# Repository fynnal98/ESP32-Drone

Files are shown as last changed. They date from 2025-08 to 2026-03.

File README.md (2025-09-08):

# ESP32-Drone
## Project Images



 

---
## Software
The code is structurd in modules:

**main**  
- Init: SBUS, IMU, PWM, LED, Battery  
- Safety: Failsafe, Low-voltage, Arming  
- Motor mix: Inputs + PID corrections  
**SbusReceiver**  
- Reads SBUS signal  
- Maps + filters channels  
- Deadband, scaling, failsafe check  

**MPU6050**  
- Reads gyro + accel  
- Complementary filter for roll/pitch  
- Provides orientation data  

**PidController**  
- Generic PID loop  
- Used for roll and pitch stabilization  (no yaw!)

**FlightController**  
- Reads roll/pitch targets from SBUS and actual values from IMU  
- Runs PID controllers for roll and pitch  
- Outputs correction values (but the Donelogic is used in main yet.)

**config.h**  
- Pin definitions  
- PID parameters  
- PWM setup  
- Battery thresholds 

---
## Hardware

Hardware:  
- ESP32-C3  
- MPU6050 // MPU6500  
- SBUS Receiver (serial data from RadioLink remote controller)  
- 4 × Brushed DC Motors (3.7 V)  
- Custom Motor Drivers (MOSFET + gate resistor + pull-down + Schottky diode)  
- 1S LiPo Battery  
- Resistor Divider (for battery voltage measurement)  
- LED Indicator (low-voltage warning)  
- Capacitors for voltage spikes  

The system is based on an ESP32-C3 Super Mini microcontroller combined with an MPU6500 IMU for orientation sensing.  
Remote control signals are received by a serial SBUS input.  
Four DC brushed motors are controlled by custom motor drivers. Each is build with a Mosfet, pulldown resisitor and a shottky diode.

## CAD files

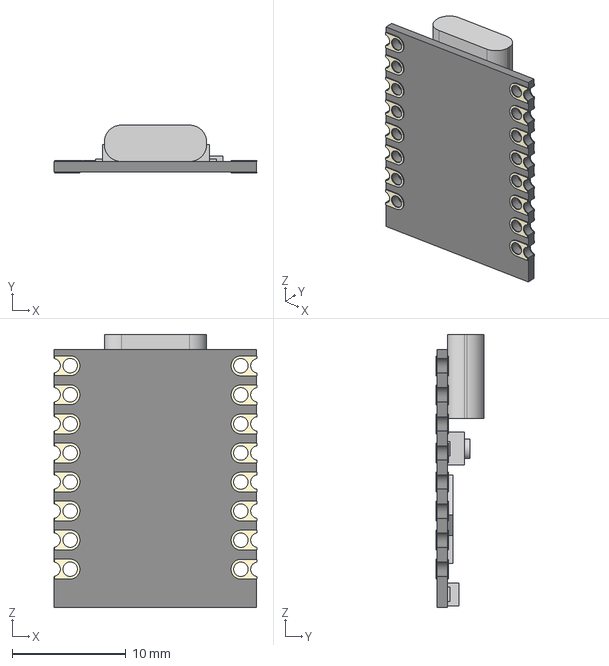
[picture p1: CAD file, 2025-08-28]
Hardware/CAD/V4/extern/ESP32-C3 supermini v5/ESP32-C3 supermini v5.step
17.8 x 4.20 x 24.0 mm

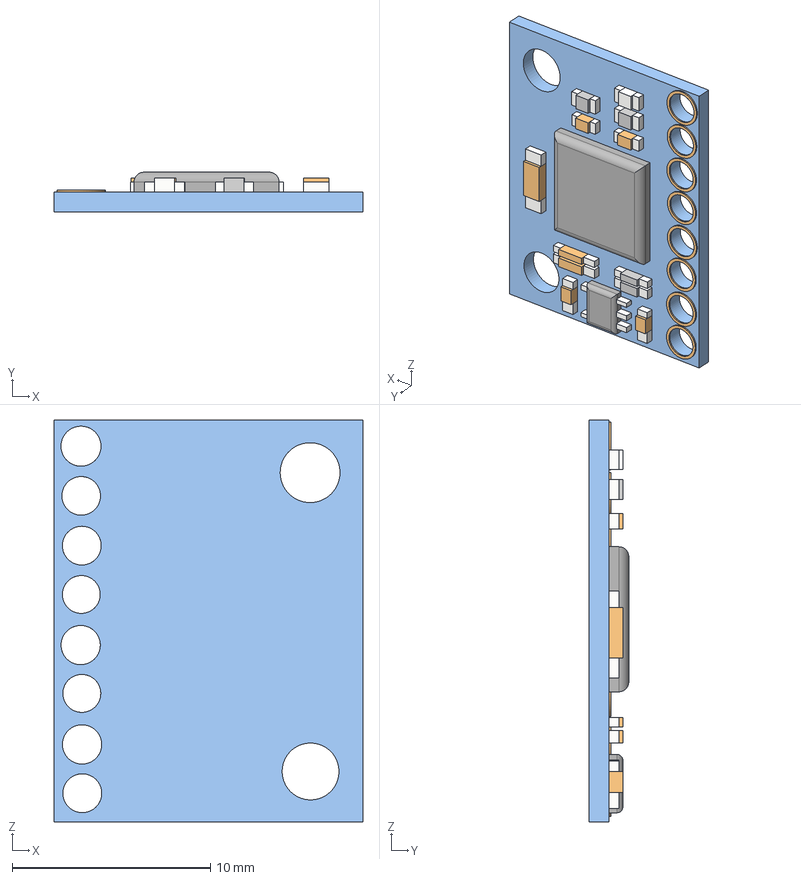
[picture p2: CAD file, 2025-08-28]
Hardware/CAD/V4/extern/MPU6050 v2/MPU6050 v2.step
15.6 x 2.00 x 20.3 mm

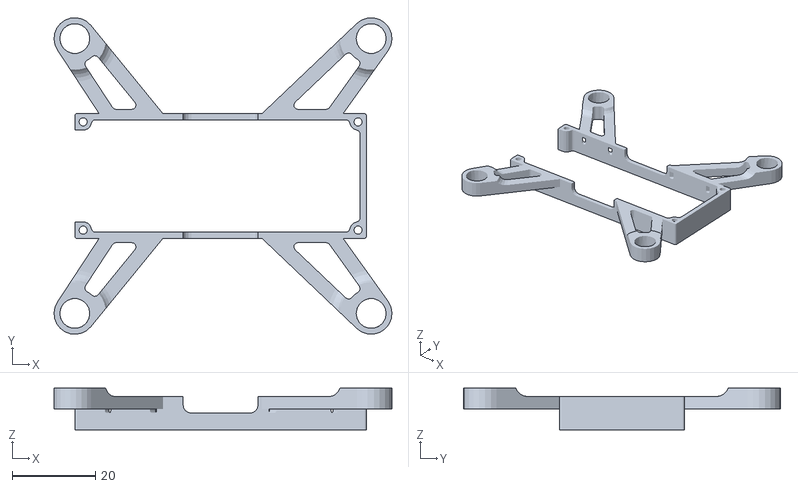
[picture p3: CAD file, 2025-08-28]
Hardware/CAD/V4/print/P_DroneCase.stl
81.1 x 76.0 x 10.0

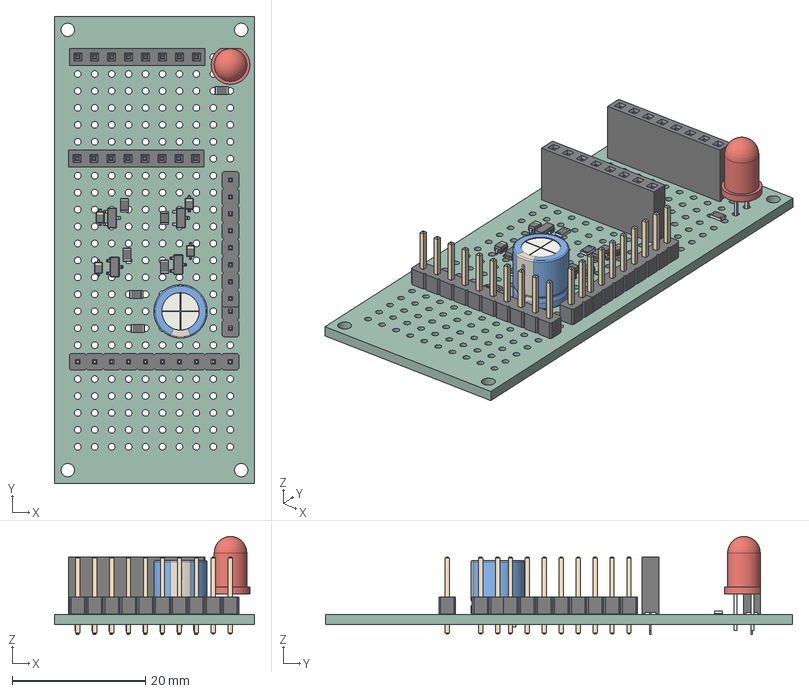
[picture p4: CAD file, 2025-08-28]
Hardware/PCB/MiniDroneFlightcontroller/MiniDroneFlightcontroller.step
30.0 x 70.0 x 14.7 mm
SOT-23 x 4
R_0805_2012Metric x 7
D_SOD-323 x 4
PinSocket_1x08_P2.54mm_Vertical x 2
CP_Radial_D8.0mm_P5.00mm
PinHeader_1x02_P2.54mm_Vertical
LED_D5.0mm
PinHeader_1x10_P2.54mm_Vertical
PinHeader_1x08_P2.54mm_Vertical
MiniDroneFlightcontroller_PCB

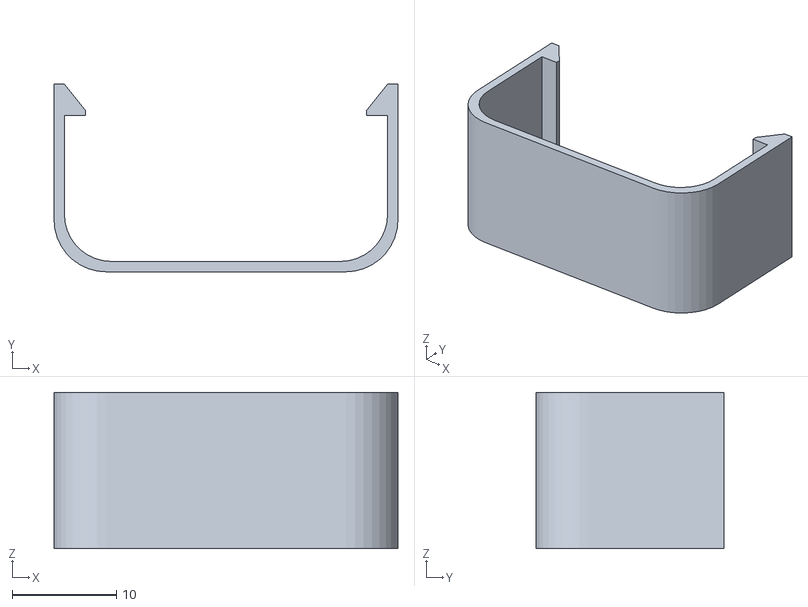
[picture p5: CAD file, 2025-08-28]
Hardware/CAD/V4/print/P_Halter.stl
33.0 x 18.0 x 15.0

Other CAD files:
Hardware/CAD/V1/OldVersions/A_MiniDrone.0048.iam
Hardware/CAD/V1/OldVersions/P_Akku_1S.0003.ipt
Hardware/CAD/V1/OldVersions/P_DroneCase.0054.ipt
Hardware/CAD/V1/P_Prop.ipt
Hardware/CAD/V2/OldVersions/A_MiniDrone.0068.iam
Hardware/CAD/V2/OldVersions/P_DroneCase.0111.ipt
Hardware/CAD/V2/OldVersions/P_Halter.0005.ipt
Hardware/CAD/V2/P_Prop.ipt
Hardware/CAD/V3/A_MiniDrone.iam
Hardware/CAD/V3/OldVersions/A_MiniDrone.0080.iam
Hardware/CAD/V3/OldVersions/P_Akku_1S.0004.ipt
Hardware/CAD/V3/OldVersions/P_DroneCase.0149.ipt
Hardware/CAD/V3/OldVersions/P_Halter.0007.ipt
Hardware/CAD/V3/OldVersions/P_Prop.0006.ipt
Hardware/CAD/V3/OldVersions/P_Prop_4_blade.0007.ipt
Hardware/CAD/V3/OldVersions/P_R6DSM.0010.ipt
Hardware/CAD/V3/P_Akku_1S.ipt
Hardware/CAD/V3/P_DroneCase.ipt
Hardware/CAD/V3/P_Halter.ipt
Hardware/CAD/V3/P_Motor.ipt
Hardware/CAD/V3/P_Motordriver.ipt
Hardware/CAD/V3/P_Prop_4_blade.ipt
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

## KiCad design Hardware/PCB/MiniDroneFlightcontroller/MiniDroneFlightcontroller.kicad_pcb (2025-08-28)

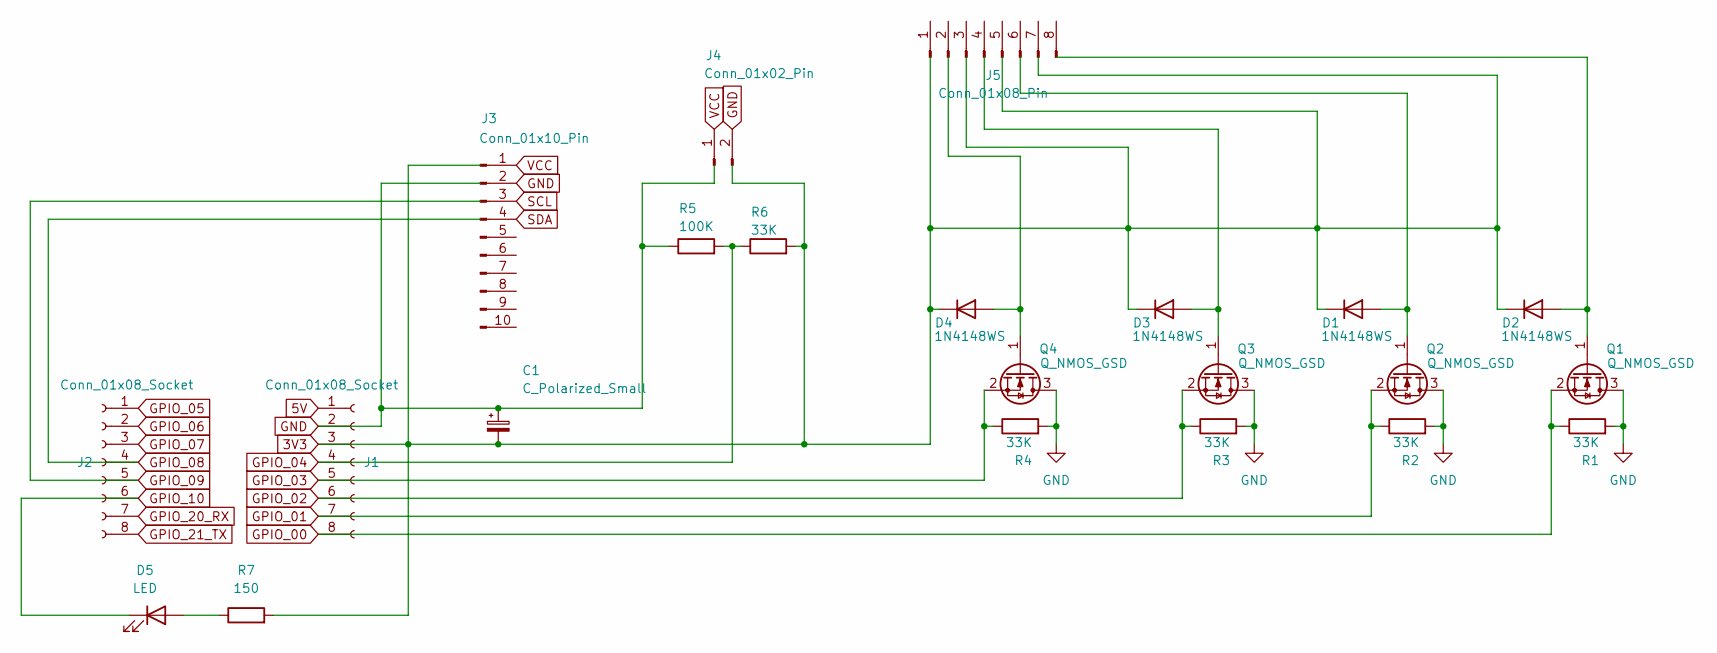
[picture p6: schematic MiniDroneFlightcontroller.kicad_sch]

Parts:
C1: C_Polarized_Small; CP_Radial_D8.0mm_P5.00mm
D1, D2, D3, D4: 1N4148WS; D_SOD-323
D5: LED; LED_D4.0mm
J1, J2: Conn_01x08_Socket; PinSocket_1x08_P2.54mm_Vertical
J3: Conn_01x10_Pin; PinHeader_1x10_P2.54mm_Vertical
J4: Conn_01x02_Pin; PinHeader_1x02_P2.54mm_Vertical
J5: Conn_01x08_Pin; PinHeader_1x08_P2.54mm_Vertical
Q1, Q2, Q3, Q4: Q_NMOS_GSD; SOT-23
R1, R2, R3, R4, R6: 33K; R_0805_2012Metric
R5: 100K; R_0805_2012Metric
R7: 150; R_0805_2012Metric

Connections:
3V3: C1.2, D1.1 (K), D2.1 (K), D3.1 (K), D4.1 (K), J1.3, R6.2, R7.2
5V: J1.1
GND: C1.1, J1.2, J3.2, J4.2, Q1.3 (D), Q2.3 (D), Q3.3 (D), Q4.3 (D), R1.2, R2.2, R3.2, R4.2, R5.1
GPIO_00: J1.8, Q1.2 (S), R1.1
GPIO_01: J1.7, Q2.2 (S), R2.1
GPIO_02: J1.6, Q3.2 (S), R3.1
GPIO_03: J1.5, Q4.2 (S), R4.1
GPIO_04: J1.4, R5.2, R6.1
GPIO_05: J2.1
GPIO_06: J2.2
GPIO_07: J2.3
GPIO_08: J2.4
GPIO_09: J2.5
GPIO_10: D5.1 (K), J2.6
GPIO_20_RX: J2.7
GPIO_21_TX: J2.8
unnamed: D1.2 (A), Q2.1 (G)
unnamed: D2.2 (A), Q1.1 (G)
unnamed: D3.2 (A), Q3.1 (G)
unnamed: D4.2 (A), Q4.1 (G)
unnamed: D5.2 (A), R7.1
SCL: J3.3
SDA: J3.4
VCC: J3.1, J4.1

Board: 2 copper layers, 22 parts (0 on the bottom side), 14 nets, no tracks yet.

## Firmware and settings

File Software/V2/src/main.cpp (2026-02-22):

#include <Arduino.h>
#include "Config.h"
#include "SbusReceiver.h"
#include "Mpu6050.h"
#include "FlightController.h"

static SbusReceiver rc;
static Mpu6050 imu;
static FlightController fc;

static uint32_t lastMicros = 0;

// Level offsets (werden nach Boot-Delay gemittelt)
static float levelRollOffDeg = 0.0f;
static float levelPitchOffDeg = 0.0f;

static void motorsInit() {
  ledcSetup(PWM_CH_MOTOR1, PWM_FREQ, PWM_RES_BITS);
  ledcSetup(PWM_CH_MOTOR2, PWM_FREQ, PWM_RES_BITS);
  ledcSetup(PWM_CH_MOTOR3, PWM_FREQ, PWM_RES_BITS);
  ledcSetup(PWM_CH_MOTOR4, PWM_FREQ, PWM_RES_BITS);

  ledcAttachPin(PIN_MOTOR1, PWM_CH_MOTOR1);
  ledcAttachPin(PIN_MOTOR2, PWM_CH_MOTOR2);
  ledcAttachPin(PIN_MOTOR3, PWM_CH_MOTOR3);
  ledcAttachPin(PIN_MOTOR4, PWM_CH_MOTOR4);

  ledcWrite(PWM_CH_MOTOR1, 0);
  ledcWrite(PWM_CH_MOTOR2, 0);
  ledcWrite(PWM_CH_MOTOR3, 0);
  ledcWrite(PWM_CH_MOTOR4, 0);
}

static void motorsOff() {
  ledcWrite(PWM_CH_MOTOR1, 0);
  ledcWrite(PWM_CH_MOTOR2, 0);
  ledcWrite(PWM_CH_MOTOR3, 0);
  ledcWrite(PWM_CH_MOTOR4, 0);
}

static void motorsWrite(const MotorOutputs& m) {
  const uint32_t d1 = (uint32_t)(m.m1 * (float)PWM_MAX);
  const uint32_t d2 = (uint32_t)(m.m2 * (float)PWM_MAX);
  const uint32_t d3 = (uint32_t)(m.m3 * (float)PWM_MAX);
  const uint32_t d4 = (uint32_t)(m.m4 * (float)PWM_MAX);

  ledcWrite(PWM_CH_MOTOR1, d1);
  ledcWrite(PWM_CH_MOTOR2, d2);
  ledcWrite(PWM_CH_MOTOR3, d3);
  ledcWrite(PWM_CH_MOTOR4, d4);
}

static void bootDelayAndCalibrate() {
  // 1) Delay damit du die Drohne sauber hinlegen kannst
  const uint32_t waitMs = BOOT_WAIT_MS;
  Serial.printf("BOOT: Warte %lums zum Hinlegen...\n", (unsigned long)waitMs);
  uint32_t t0 = millis();
  while (millis() - t0 < waitMs) {
    motorsOff();
    delay(50);
  }

  // 2) Gyro kalibrieren (Drohne muss ruhig liegen)
  if (imu.isConnected()) {
    Serial.println("BOOT: Gyro Kalibrierung (ruhig liegen lassen)...");
    imu.calibrate(600);
    Serial.println("BOOT: Gyro Kalibrierung fertig");
  }

  // 3) Level-Offset mitteln (Roll/Pitch Null setzen)
  //    (nur sinnvoll, wenn rollDeg/pitchDeg aus Acc+Gyro kommen)
  if (imu.isConnected()) {
    Serial.println("BOOT: Level-Offset messen (still & level)...");
    const uint32_t levelMs = LEVEL_CAL_MS;
    uint32_t start = millis();
    uint32_t n = 0;
    float sumR = 0.0f, sumP = 0.0f;

    // kleine dt Updates, damit roll/pitch frisch sind
    uint32_t last = micros();
    while (millis() - start < levelMs) {
      uint32_t now = micros();
      float dt = (float)(now - last) / 1000000.0f;
      last = now;
      if (dt < DT_MIN) dt = DT_MIN;
      if (dt > DT_MAX) dt = DT_MAX;

      imu.update(dt);
      sumR += imu.rollDeg();
      sumP += imu.pitchDeg();
      n++;
      motorsOff();
      delay(5);
    }

    if (n > 0) {
      levelRollOffDeg = sumR / (float)n;
      levelPitchOffDeg = sumP / (float)n;
    }
    Serial.printf("BOOT: Level-Offset gesetzt rollOff=%.2f pitchOff=%.2f\n",
                  levelRollOffDeg, levelPitchOffDeg);
  }
}

void setup() {
  Serial.begin(115200);
  delay(200);

  motorsInit();
  rc.begin();

  const bool imuOk = imu.begin(IMU_SDA_PIN, IMU_SCL_PIN);
  if (!imuOk) {
    Serial.println("MPU6050 NICHT gefunden");
  } else {
    Serial.println("MPU6050 OK");
  }

  // PID config (falls du das nutzt)
  fc.setConfig(FC_CFG);
  fc.begin();

  bootDelayAndCalibrate();

  lastMicros = micros();
}

void loop() {
  const uint32_t nowUs = micros();
  const uint32_t periodUs = 1000000UL / LOOP_HZ;

  if ((uint32_t)(nowUs - lastMicros) < periodUs) {
    delayMicroseconds(30);
    return;
  }

  float dt = (float)(nowUs - lastMicros) / 1000000.0f;
  lastMicros = nowUs;
  if (dt < DT_MIN) dt = DT_MIN;
  if (dt > DT_MAX) dt = 1.0f / (float)LOOP_HZ;

  rc.update();

  if (rc.signalLost()) {
    motorsOff();
    fc.reset();
    return;
  }

  if (imu.isConnected()) {
    imu.update(dt);
  }

  static bool armed = false;
  const bool armSwitch = rc.armed();
  const float thr = rc.throttle();

  if (!armSwitch) {
    armed = false;
    motorsOff();
    fc.reset();
    return;
  }

  if (!armed) {
    motorsOff();
    fc.reset();
    if (thr < THROTTLE_MIN_ARM) {
      armed = true;
      fc.reset();
    }
    return;
  }

  if (thr < THR_CUTOFF) {
    motorsOff();
    fc.reset();
    return;
  }

  // WICHTIG: Offsets übergeben
const MotorOutputs m = fc.update(rc, imu, dt, armed, levelRollOffDeg, levelPitchOffDeg);  motorsWrite(m);

Serial.printf("Rlvl=%.2f Plvl=%.2f\n",
              imu.rollDeg() - levelRollOffDeg,
              imu.pitchDeg() - levelPitchOffDeg);
}

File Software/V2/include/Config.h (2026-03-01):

#pragma once
#include <stdint.h>

// === Boot / Calibration Timing ===
static constexpr uint32_t BOOT_WAIT_MS = 3000;        // Zeit zum Hinlegen nach Akku
static constexpr uint32_t LEVEL_CAL_MS = 1500;        // Dauer Level-Mittelung

/* =========================
 * SBUS
 * ========================= */
static constexpr int SBUS_RX_PIN     = 20;
static constexpr bool SBUS_INVERTED  = true;
static constexpr uint32_t SBUS_SIGNAL_TIMEOUT_MS = 300;

static constexpr int SBUS_INPUT_MIN = 307;
static constexpr int SBUS_INPUT_MAX = 1693;

/* Channel mapping (Radiolink typisch) */
static constexpr int CH_ROLL     = 0; // CH1
static constexpr int CH_PITCH    = 1; // CH2
static constexpr int CH_THROTTLE = 2; // CH3
static constexpr int CH_YAW      = 3; // CH4
static constexpr int CH_ARM      = 9; // AUX

/* RC shaping */
static constexpr float RC_DEADBAND     = 0.03f;
static constexpr float RC_SMOOTH_ALPHA = 0.85f;

/* =========================
 * IMU (MPU6050)
 * ========================= */
static constexpr int IMU_SDA_PIN = 6;
static constexpr int IMU_SCL_PIN = 7;

static constexpr float COMP_ALPHA = 0.98f;

/* =========================
 * Motors / Pins
 * ========================= */
static constexpr int PIN_MOTOR1 = 5;
static constexpr int PIN_MOTOR2 = 2;
static constexpr int PIN_MOTOR3 = 3;
static constexpr int PIN_MOTOR4 = 4;

/* =========================
 * PWM (LEDC) — dein funktionierendes Setup
 * ========================= */
static constexpr uint32_t PWM_FREQ     = 12000;
static constexpr uint8_t  PWM_RES_BITS = 10;
static constexpr uint32_t PWM_MAX      = (1u << PWM_RES_BITS) - 1u;

static constexpr int PWM_CH_MOTOR1 = 0;
static constexpr int PWM_CH_MOTOR2 = 1;
static constexpr int PWM_CH_MOTOR3 = 2;
static constexpr int PWM_CH_MOTOR4 = 3;

/* =========================
 * Control Loop
 * ========================= */
static constexpr uint32_t LOOP_HZ = 500;
static constexpr float DT_MIN = 1.0f / 2000.0f;
static constexpr float DT_MAX = 1.0f / 50.0f;

/* Stabilize */
static constexpr float MAX_ANGLE_DEG = 15.0f;

/* Rate limits */
static constexpr float MAX_RATE_ROLL_DPS  = 350.0f;
static constexpr float MAX_RATE_PITCH_DPS = 350.0f;
static constexpr float MAX_RATE_YAW_DPS   = 220.0f;

/* Safety */
static constexpr float THROTTLE_MIN_ARM = 0.02f; // arm nur bei low throttle
static constexpr float THR_CUTOFF       = 0.01f; // darunter: motor off + pid reset
static constexpr float THROTTLE_IDLE    = 0.050f; // erst aktiv wenn thr > cutoff
static constexpr float THROTTLE_MAX     = 0.95f; // headroom fürs Mixing

/* Mixer option */
static constexpr bool MIX_SWAP_FRONT_BACK = false;


// =========================
// PID Config (tunable)
// =========================
struct PidGains {
  float kp;
  float ki;
  float kd;
  float iLimit;
  float outLimit;
};

struct FcConfig {
  // Angle (outer loop) -> outputs desired rate in deg/s
  PidGains angleRoll;
  PidGains anglePitch;

  // Rate (inner loop) -> outputs normalized correction
  PidGains rateRoll;
  PidGains ratePitch;
  PidGains rateYaw;

  // Optional: scaling for corrections at low throttle
  float corrRampFullAtThr; // e.g. 0.35f means full corrections at ~35% throttle
};

static constexpr FcConfig FC_CFG = {
  /* angleRoll  */ { 5.5f, 0.0f, 0.06f, 40.0f, 220.0f },
  /* anglePitch */ { 5.5f, 0.0f, 0.06f, 40.0f, 220.0f },

                 /* { kp   , ki   , kd     , iLimit, outLimit } */
  /* rateRoll   */ { 0.85f, 0.10f, 0.0012f, 0.90f, 1.60f },
  /* ratePitch  */ { 0.85f, 0.10f, 0.0012f, 0.90f, 1.60f },
  /* rateYaw    */ { 0.08f, 0.05f, 0.0000f, 0.40f, 0.80f },

  /* corrRampFullAtThr */ 0.06f
};


static constexpr float MOTOR_ROLL_TRIM = -0.00f;

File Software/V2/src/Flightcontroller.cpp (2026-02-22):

#include "FlightController.h"

float FlightController::clampf(float v, float lo, float hi)
{
    if (v < lo) return lo;
    if (v > hi) return hi;
    return v;
}

void FlightController::setConfig(const FcConfig &cfg)
{
    _cfg = cfg;

    // Angle
    _pidAngleRoll.setGains(cfg.angleRoll.kp, cfg.angleRoll.ki, cfg.angleRoll.kd);
    _pidAngleRoll.setLimits(cfg.angleRoll.iLimit, cfg.angleRoll.outLimit);

    _pidAnglePitch.setGains(cfg.anglePitch.kp, cfg.anglePitch.ki, cfg.anglePitch.kd);
    _pidAnglePitch.setLimits(cfg.anglePitch.iLimit, cfg.anglePitch.outLimit);

    // Rate
    _pidRateRoll.setGains(cfg.rateRoll.kp, cfg.rateRoll.ki, cfg.rateRoll.kd);
    _pidRateRoll.setLimits(cfg.rateRoll.iLimit, cfg.rateRoll.outLimit);

    _pidRatePitch.setGains(cfg.ratePitch.kp, cfg.ratePitch.ki, cfg.ratePitch.kd);
    _pidRatePitch.setLimits(cfg.ratePitch.iLimit, cfg.ratePitch.outLimit);

    _pidRateYaw.setGains(cfg.rateYaw.kp, cfg.rateYaw.ki, cfg.rateYaw.kd);
    _pidRateYaw.setLimits(cfg.rateYaw.iLimit, cfg.rateYaw.outLimit);
}

void FlightController::begin()
{
    reset();
}

void FlightController::reset()
{
    _pidAngleRoll.reset();
    _pidAnglePitch.reset();

    _pidRateRoll.reset();
    _pidRatePitch.reset();
    _pidRateYaw.reset();
}

float FlightController::angleToRate(float angleSetDeg, float angleMeasDeg, Pid &anglePid, float dt)
{
    // output: deg/s
    return anglePid.update(angleSetDeg, angleMeasDeg, dt);
}

float FlightController::rateControl(float rateSetDps, float rateMeasDps, Pid &ratePid, float dt)
{
    // output: normalized correction (Mixer-Units)
    return ratePid.update(rateSetDps, rateMeasDps, dt);
}

MotorOutputs FlightController::update(SbusReceiver &rc,
                                      const Mpu6050 &imu,
                                      float dt,
                                      bool armed,
                                      float levelRollOffsetDeg,
                                      float levelPitchOffsetDeg)
{
    MotorOutputs out{};

    if (!armed)
    {
        return out;
    }

    // Throttle 0..1
    float thr = clampf(rc.throttle(), 0.0f, 1.0f);

    // Unter Cutoff: Motoren AUS + keine Regelung
    if (thr < THR_CUTOFF)
    {
        return out;
    }

    // Throttle auf Idle..THROTTLE_MAX skalieren (Headroom fürs Mixing)
    const float thrScaled = clampf(
        THROTTLE_IDLE + thr * (THROTTLE_MAX - THROTTLE_IDLE),
        0.0f, 1.0f);

    // Korrekturen bei niedrigem Throttle sanft hochfahren
    float rampDen = _cfg.corrRampFullAtThr;
    if (rampDen < 0.05f) rampDen = 0.05f; // Schutz
    float corrScale = (thr - THR_CUTOFF) / rampDen;
    corrScale = clampf(corrScale, 0.0f, 1.0f);

    // Stick -> Angle Sollwert (Angle Mode)
    const float rollSetDeg  = rc.roll()  * MAX_ANGLE_DEG;
    const float pitchSetDeg = rc.pitch() * MAX_ANGLE_DEG;

    // Gemessene Winkel (mit Level-Offset)
    const float rollMeasDeg  = imu.rollDeg()  - levelRollOffsetDeg;
    const float pitchMeasDeg = imu.pitchDeg() - levelPitchOffsetDeg;

    // Angle -> Rate Sollwerte (deg/s), begrenzen
    const float rollRateSet = clampf(
        angleToRate(rollSetDeg, rollMeasDeg, _pidAngleRoll, dt),
        -MAX_RATE_ROLL_DPS, MAX_RATE_ROLL_DPS);

    const float pitchRateSet = clampf(
        angleToRate(pitchSetDeg, pitchMeasDeg, _pidAnglePitch, dt),
        -MAX_RATE_PITCH_DPS, MAX_RATE_PITCH_DPS);

    // Yaw: direkt Rate Sollwert aus Stick
    const float yawRateSet = rc.yaw() * MAX_RATE_YAW_DPS;

    // Rate PIDs (Gyro rates)
    float rollCorr  = rateControl(rollRateSet,  imu.gyroX_dps(), _pidRateRoll,  dt);
    float pitchCorr = rateControl(pitchRateSet, imu.gyroY_dps(), _pidRatePitch, dt);
    float yawCorr   = rateControl(yawRateSet,   imu.gyroZ_dps(), _pidRateYaw,   dt);

    // Low-throttle scaling
    rollCorr  *= corrScale;
    pitchCorr *= corrScale;
    yawCorr   *= corrScale;
    
    rollCorr += MOTOR_ROLL_TRIM;


    // QUADX Mixer:
    // (m1..m4 sind "normalized motor commands" 0..1 nach clamp)
    float m1 = thrScaled + pitchCorr + rollCorr - yawCorr;
    float m2 = thrScaled + pitchCorr - rollCorr + yawCorr;
    float m3 = thrScaled - pitchCorr - rollCorr - yawCorr;
    float m4 = thrScaled - pitchCorr + rollCorr + yawCorr;

    // Optional: Front/Back swap (wenn Layout/Belegung vertauscht ist)
    if (MIX_SWAP_FRONT_BACK)
    {
        const float t1 = m1, t2 = m2;
        m1 = m4; m2 = m3; m3 = t2; m4 = t1;
    }

    out.m1 = clampf(m1, 0.0f, 1.0f);
    out.m2 = clampf(m2, 0.0f, 1.0f);
    out.m3 = clampf(m3, 0.0f, 1.0f);
    out.m4 = clampf(m4, 0.0f, 1.0f);

    return out;
}

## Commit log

2026-02-21 change to esp32c
    [A_MiniDrone.0080.iam, A_MiniDrone.0134.iam, A_MiniDrone.iam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]
2026-02-21 low filter
